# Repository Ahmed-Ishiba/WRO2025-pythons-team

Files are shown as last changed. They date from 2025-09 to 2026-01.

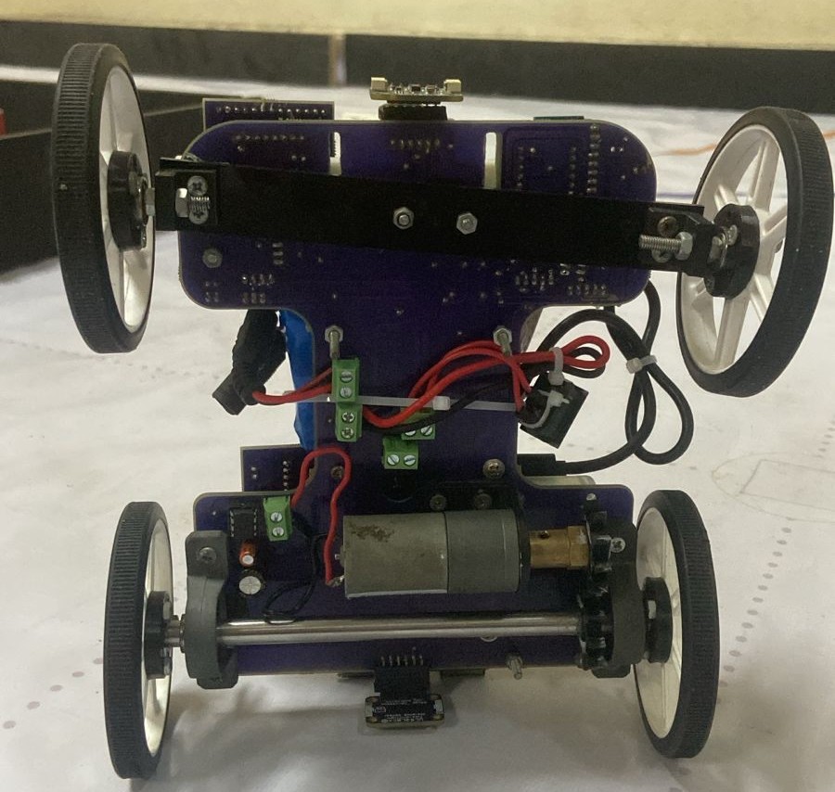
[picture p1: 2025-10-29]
Team&Robot Photos/Undeer_view.jpeg

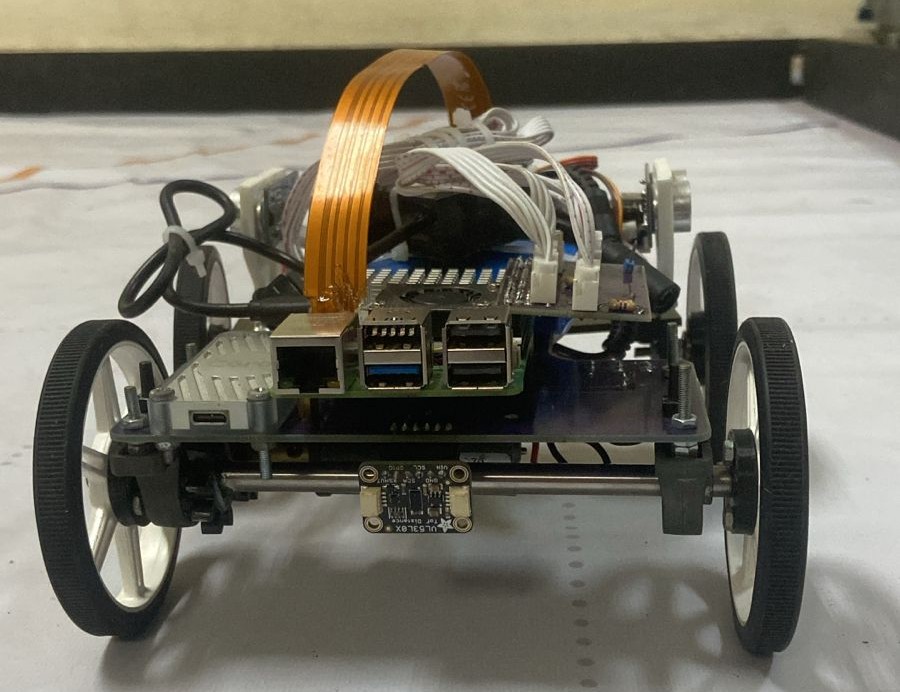
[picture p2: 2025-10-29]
Team&Robot Photos/Back_photo.jpeg

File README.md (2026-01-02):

<p align="center">
mainThepythons-removebg-preview
</p>

<p align="center">
  <a href="https://www.the-pythons.com/" target="_blank">
    
  </a>
  <a href="mailto:ahmedishiba9@gmail.com">
    
  </a>
  <a href="https://github.com/ahmed-ishiba">
    
  </a>
   <a href="https://github.com/Thesuperiornour">
    
  </a>
  <a href="https://github.com/Eyad005">
    
  </a>
  <a href="https://www.youtube.com/@thepythonseg">
    
  </a>
</p>  

Documentation of our self-driving car for the **WRO 2025 Future Engineers** category.

Our team members:
- **Ahmed Ibrahim Elsayed** — Software lead  
- **Eyad Ahmed Nazary** — Electrical lead  
- **Nour Eldin Raoof** — Mechanical design & fabrication  
- **Omar Khaled** — Coach and mentor  

---

## Content

1. [Project Overview](#project-overview)  
    1. [What is WRO?](#what-is-wro)  
    2. [Team Introduction](#team-introduction)  
    3. [Our Mission](#our-mission)  
2. [System Design](#system-design)  
    1. [Robot Architecture](#robot-architecture)  
    2. [Design Philosophy](#design-philosophy)  
    3. [System Diagram](#system-diagram)  
    4. [Bill of Materials](#bill-of-materials)  
3. [Hardware](#hardware)  
    1. [Mechanical](#mechanical)  
    2. [Electrical](#electrical)  
4. [Software](#software)  
    1. [Brief Overview](#brief-overview)  
    2. [Code flow chart](#flow-chart)  
5. [MATLAB Modeling & Simulation](#modelling-and-simulation)  
    1. [Model Overview](#model-overview)  
    2. [Problem Context and Strategy](#problem-context-and-strategy)  
    3. [Modeling and Simulation](#modelling-and-simulation)
        1. [Simulink Logical Model](#simulink-logical-model)
        2. [Complementary Filter Subsystem](#complementary-filter-sub-system)
        3. [Stateflow Diagram](#state-flow-diagram)
        4. [MATLAB Function](#matlab-function)
        5. [Simscape Electrical Model](#simscape-electrical-model)  
    4. [Testing and Verification](#testing-and-verification)  
6. [Testing & Calibration](#testing-and-calibration)
7. [Reproduce Our Robot: Step-by-Step Guide](#reproduce-our-robot)
8. [Future Improvements](#future-improvements)
9. [Team photo](#team-photo)  

## Project Overview

### What is WRO?

WRO (World Robot Olympiad), specifically the **Future Engineers** category, is a competition created to foster passion for STEM. The Future Engineers category is designed for university students. The challenge changes every 3 years, and this year the theme is **autonomous driving**.  
The robot must be designed to drive around a track **completely autonomously**, without external human intervention.

### Team Introduction

We are the **third generation** of *The Pythons* team.  
Our team consists of 3 members and a coach:

1. **Ahmed Ibrahim Elsayed (me):** Software lead — 2nd year, Faculty of Engineering, Alexandria University  
2. **Eyad Ahmed Nazary:** Electrical lead — 1st year, AASTMT  
3. **Nour Eldin Raoof:** Mechanical lead — 3rd year, Faculty of Science, Alexandria University  
4. **Omar Khaled:** Team coach — AASTMT

We have been participating in robotics competitions since **2016**, and we joined The Pythons team in **2017**.

### Our Mission

Our main mission in robotics competitions is to **improve ourselves**, gain experience, and meet like-minded people.  
We specifically enjoy WRO because it **encourages open-source work**, allowing teams to learn from each other, share solutions, and build stronger communities.
.
## System Design:
  ### Robot architecture:   
The main input sources are the camera, ultrasonic sensors to measure distance from walls, Time Of Flight sensors to measure distance from obstacles and parking lot walls, MPU6050 sensor to measure orientation angle for corner rotation and to ensure parallel parking.  
Then the raspberry pi processes these input data and outputs character to KB2040 to control servo and DC motors

  ### Design philosophy:
  When designing our robot we always made sure that our design follows a modular design that is easy to comprehend and troubleshoot, which helps us in improving it with ease, this approach also minimizes time delays that may happen due to fabrication and unfortunate mishaps, this also helps anyone without experience in robotics and future teams to pick up where we left off.
  ### System diagram:  
system_diagram_main drawio

This diagram shows the main components of the robot and how they communicate.  
- The Raspberry Pi 5 acts as the central controller, running the main software and decision-making algorithms.  
- It communicates with ESP32 microcontroller and KB2040 via UART.  
- The KB2040 handles all real-time tasks such as controlling the servo and DC motors through PWM signals.  
-  All controllers share a common power source with independent voltage regulation for stability.

<br>  

  ### Bill Of Materials:   
  
| Component Name | Number of Items | Price (EGP) | Price (USD) |
|---|---|---|---|
| Google Coral Accelerator | x1 | 6,250.00 | 125.00 |
| ESP32 Supermini | x1 | 350.00 | 7.00 |
| KB2040 | x1 | 425.00 | 8.50 |
| Raspberry Pi 5 | x1 | 4,000.00 | 80.00 |
| IMU MPU6050 | x1 | 125.00 | 2.50 |
| Step Down Converter 12V→5V | x1 | 450.00 | 9.00 |
| Wheels | x4 | 473.00 | 9.45 |
| Motor | x1 | 350.00 | 7.00 |
| Servo (180°) | x1 | 150.00 | 3.00 |
| Arducam | x1 | 3,000.00 | 60.00 |
| Step Down Converter 12V→3.3V | x2 | 35.00 | 0.70 |
| 12V Battery | x1 | 450.00 | 9.00 |
| Ultrasonic Sensor | x2 | 45.00 | 0.90 |
| Motor Driver IC | x1 | 100.00 | 2.00 |
| Big Ball Bearings | x2 | 100.00 | 2.00 |
| Small Ball Bearings | x2 | 50.00 | 1.00 |
| PCB Fabrication | x1 | 1,250.00 | 25.00 |
|Time Of Flight sensor | x2 | _ | _ |
| **Total** | — | **17,186.50** | **363.41** |
## Hardware:
This section includes brief overview of hardware section of robot (Mechanical and electrical).  
Each section is explained in detail in it's respective folder  
SLDPRT, DXF and board files are also included in their respective folder to download, print and get down to business.  
  ### Mechanical:
  [Mechanical directory](/Mechanical/)     
  
Robot 3d Design

During the design phase, we chose to stick with a simple structure to save time on fabrication, especially after making a bold decision that I’ll discuss in the next section. Our main focus however was to maximize the steering angles achievable from the servo by creating a fully free movement system, which is vital in turning since we can turn faster and closer to the blocks than other cars. In order to follow the competition's guidelines of using only _**one**_ motor to provide the forward movement to the whole robot we created a gear system to transfer the motor's movement to the rear wheels, also creating a versatile semi movable component mounting system -as seen in the camera mounting- to eliminate the need for refabrication which in turn cuts down the time needed for assembling the robot. 

We also chose big wheels to maximize distance crossed during same revolution this also helps in faster steering.  

  ### Electrical:  
  [Electrical directory](/Electrical/)
3d_pcb  

You might’ve noticed that our PCB has a rather unusual shape — that’s because it is the shape of our mechanical design!  
This brings us to the bold decision I mentioned earlier: we chose to make the base itself the main circuit.  
This approach not only improves stability and reduces overall size by eliminating separate circuit boards, but also makes assembly incredibly straightforward — every component has its exact place.  

But wait — there’s another bold decision! Did you notice there’s no motor driver on our robot?  
That’s right — we built our own motor driver using a dedicated IC and a decoupling capacitor.  
This approach helped us further reduce the robot’s size by eliminating the need for bulky modules like the L298N or Cytron drivers.

## Software:
In this section I will also only provide overview on code and thought process since line-by-line documentation can be found in the [Software directory](/Software/).  

  ### Brief overview:
  For our software and programming I divided it into 3 sections: 
  - Wall tracking
  -  Obstacle Avoidance
  -  Corner detection
  -  Parking
1. Wall Tracking:
   For wall tracking I calculated wall area difference that camera sees and wall difference measured from ultrasonic sensors then used sensor fusion to get accurate data that    I then passed to a PID controller to center the robot all processed on the raspberry pi 5.
   
2. Obstacle Avoidance:
    For obstacle avoidance we used a custom trained yolov8 AI model with 500+ pictures to make sure that the robot detects the traffic signs regardless of environment.
    This approach is better than the traditional image processing approach that relies on the environment since HSV values change according to reflected light.
    Our AI model runs on the google edge TPU to achieve high FPS and faster detection.

     

  https://github.com/user-attachments/assets/0746ed6e-e767-420a-9b96-121c0c189ac0

3. Corner detection:
   For corner detection we used simple image processing algorithms that detect blue and orange strips using the HSV values of each color to apply masks
   
4. Parking:
   IN PROGRESS  
  ### Flow Chart:   

flow_chart drawio

## Modelling and simulation:
  ### Model Overview:  
  Here we will not go into much detail, you can find a detailed explanation, model files and statflow files in the [Modelling and simulation directory](/Modeling%20and%20simulation/)  
  </br>
  When designing our wall centering algorithm we used the simplest algorithm possible due to how hard it is to tune advanced control algorithms like PID or applying filters, however when MathWorks created this award we had no reason not to use it and apply any algorithm we wanted especially after giving us license for the newest MATLAB version for free.  
  </br>
  now we can apply all the algorithms we want and all my crazy ideas, here is what we did:  
  When centering in the previous algorithm we only used the area of the 2 walls seen by our arducam however it was really noisy and changes too fast which is not that good for wall centering, however when we tried to use an ultrasonic sensor the distance readings where precise but the rate at which it changes was really slow  
  </br>
  so now we have 2 methods to measure the same thing each have their pros and cons so we got the idea to fuse them both with a simple weighted sum formula so we can have control over it and ensure it's smoothness  
  
  After we get the result of the formula which measures the deviation of the robot from the center of the lane we then pass it into a PID controller then we take the output of the controller and pass it into a map function that we implemented myself in order to convert the range of the PID output into a range that my servo accepts(from 0 to 180)  
  
  ### Problem context and strategy:  
  the main challenges that we faced were:  
  - Creating the weighted sum formula and tuning the weights
  - Tuning the PID
  - Making sure the map function works correctly
  - and a problem that we realised later is that I don't know how to test this!
  - simulating our electrical system on simscape electrical  

  As for our strategy:   
  1. we started by writing pseudo code for my algorithm and knew it's building blocks
  2. For simplicity we divided this algorithm into 5 parts: the complementary filter, the PID controller, the map function, creating a stateflow diagram and simulating the circuit we then tackled each in this order
  3. we then decided what MathWorks products help with this which were: Simulink for creating a subsystem for my filter and use it's wide variety of blocks to save time on implementing a PID algorithm from scratch, MATLAB for writing code of our mapping function, simscape electrical for simulating my electrical system and stateflow for creating a diagram of my algorithm using states  
  </br>   
  Using MATLAB, Simulink, simscape and state flow saved so much time and were extremely helpful   

  - using MATLAB for writing the mapping code was extremely easy especially with MATLAB's easy syntax
  - Simulink was by far the best tool we used because not only can we tune algorithms and filters without needing any hardware we can just tune it with only clicking one button! not to mention the clear modular look that helped me troubleshoot where exactly our model went wrong, the graphing that helps us understand the behaviour of our robot and derive meaningful data from it and realizing logical problems in minutes that would've taken days to realize
  - stateflow was really helpful in dividing the algorithm like a flow chart but much briefly, helped us in verifying my code since the code is divided into states just like stateflow and it also helped us in verifying condition if changing states and overall is a vital tool
  - simscape electric was used for simulating our circuit and finding out stall current, max current draw and we used it to correct our choice of battery since we kept having power issues but using simscape we corrected a mistake that would've cost us the competition, this is also a tool that we would definitely use for future robotics projects

  ### Modelling and simulation:  
  #### Simulink logical model:  
  
  now for the main model as I said everything is explained in detail in the [Modelling directory.](/Modeling%20and%20simulation/)  
  simulink_model  

  This is the main model and as you can see we take input from 2 sources that somewhat measure the same thing then pass it into our complementary filter that outputs an estimated deviation from the center of the lane and passes it to a PID controller and finally map it to servo range using the map function and send it to the servo  
  
 this algorithm is from my perspective as simple as it gets while at the same time maintaining it's simplicity for fast and easy troubleshooting (not that there is room for error after tuning it)  

#### Complementary filter sub-system:  

 For the complementary filter we created a sub-system for it which is by far the most useful feature in simulink since the logic for the filter is very confusing when put with the main system, here is the diagram for the complementary filter (explained in detail in the modelling directory):  
 
  filter_subsystem  

#### State-flow diagram:   

  Here is the stateflow diagram for you to understand how our code is divided  

  stateflow_chart     

#### MATLAB function:   

Here is the mapping function we implemented which is just a mathematical formula nothing too complicated   

mapping_function

#### Simscape electrical model:   
We used simscape electrical to measure our maximum ampere consumption, required voltage and suitable battery capacity, here is a photo of our model:   

model

  ### Testing and verification:   
  #### Testing Logical model:   
  
  For testing this model we had to think and come up with ideas we then came to the conclusion to use the simulink function generator  
  
  we used a sin wave to simulate changing input and we of course got an output in shape of sin wave which is both scientifically and physically correct since this model is considered a linear time-invariant system so only the amplitude changes and physically correct since when error increases from the setpoint(the rise of the sine wave) the output should also increase to compensate and correct this error  

  model_using_sine  

  complementary_filter_and_pid  

this is the graph of the complementary filter and the PID controller and above it is the model but we used the sin generator as the input.

  

This is the output(servo degree) resulting from the model and as you can see it changes reasonably with the changing the input both following the same graph  

</br>
We also used step function generator to simulate specific cases that I encountered when working on my robot and coincidentally found them

model_using_step  

step_output

this is the output (servo degree) resulting from our model and above it is the model using the step function generator  

</br>

#### Testing the electrical model:  

As for testing our electrical model it was as easy as hitting run then seeing the output voltage and current intensity on our scope  

volt_intemsity  

 As you can see we got a max current draw of 7 Amps and voltage of approximately 11.1 volts so we made our decision for battery type by dividing available battery capacities on the internet by the max current and getting how long it will last.  

## Testing and calibration:
After completing the robot assembly, we performed a series of tests to ensure that every subsystem was functioning correctly.
We ran the test scripts located in the [Software Testing Directory](/Software/System%20Testing/)

- Communication between the microcontrollers and sensors
- Sensor testing and calibration
- Motor operation and direction control
- Servo steering response
- Camera functionality and data transmission

## Reproduce Our Robot:  
A [Raspberry pi setup script](/raspberrypi_setup.sh) is included that setups all required packages 
1. First start with the main body of robot (after buying components of course)
2. Fabricate the pcb since this is the body or if you want to wire everything and don't need a pcb just download our solidworks files and cnc cut it
3. assemble the robot by connecting everything to the pcb like labeled in our fusion360 file or connect using jumper wires
4. setup the raspberry pi and enable i2c and uart
5. clone this repo on raspberry pi
6. test the system using the files in the [Software testing directory](/Software/System%20Testing/)
7. After making sure every component in the system is running normally, run the main code
8. Now you have a working WRO Future engineers self-driving car!

## Future improvements:
In the future if we participate again and for other teams looking at this repo here are some improvements I wished to implement:
- Use better sensor fusion algorithms
- Create a Simulink environment specifically for this competition like the one in robotics playground
- Better weight distribution in the robot design
- Put built-in voltage sensor
- add cloud-based data logging for better debugging
- create a GUI that combine camera frame and terminal output (looks cool no other reason)
## Team photo:  



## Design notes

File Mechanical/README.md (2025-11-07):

# Mechanical design of robot:
## Drive System 
The Mechanical part is the first part in the process of the robot's creation, in the WRO Future Engineers category there are certain design regulating rules like size must not excede 30x30cm or that the robot's 
weight must not excede 3kg and the robot must be driven wholly by one motor while these regulations seem easily applicable the last one is not to overcome that challenge we created a fully original gear system that 
features two gears that have been designed from scratch and modified specifically for our needs to provide forward motion for the robot.
Robot Rear System

### Steering System 
In the previous section i mentioned the regulation that says that whole robot's drive must be powered by just __*one*__ motor but that doesnt say the same for the steering system, we created a 120 degree of freedom steering system all connected to one servo motor, this ingenius design is very effective against even the sharpest of turns.



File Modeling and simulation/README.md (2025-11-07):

# Detailed explanation of each model 

# Table of content:  

1. [Electric model](#electric-model)
2. [Map function](#map-function)
3. [Simulink model](#simulink-model)
4. [Cool animation using robotics playground](#animation-using-robotics-playground)

## Electric model:

model  

This model represents the electrical power distribution of a small robotic system. It includes a DC battery, a buck converter for regulated low-voltage supply, an H-Bridge driving a DC motor, a servo motor subsystem, and load models representing microcontrollers and sensors. The goal is to simulate real power consumption, voltage drops, and motor behavior under different load conditions.

### 🟦 Overview of Simscape

Simscape is a MATLAB/Simulink toolbox that allows modeling using physical components rather than manual equations. Components are connected using physical conserving ports (e.g., electrical +/− terminals), ensuring simulations follow real laws like Kirchhoff’s Current/Voltage Law and mechanical rotational dynamics.  

This is useful for:   

- Testing system behavior before hardware assembly.  

- Observing current and voltage profiles.

- Evaluating different power configurations.

- Detecting instability or saturation in motor loads.

### 🔌 System Components and Their Roles   

| **Component** | **Purpose in the System** | **Important Parameters to Configure** |
| --- | --- | --- |
| DC Battery | Supplies the main power to the system, representing the real robot battery. | Nominal voltage, internal resistance, capacity (optional). |
| Buck Converter | Steps down battery voltage to a lower regulated voltage for electronics and low-power devices. | Output voltage, inductor value, capacitor value, switching frequency. |
| Constant Power Load | Models microcontrollers and sensors that draw nearly constant power regardless of voltage. | Power consumption (W), minimum operating voltage. |
| H-Bridge | Controls motor direction and speed using PWM input signals. | Control mode (PWM/Logic), supply voltage, dead-time/shoot-through protection. |
| DC Motor | Converts electrical power into mechanical rotational power. Represents drivetrain motors. | Armature resistance, back-EMF constant, rated torque, inertia. |
| Servo Motor | Provides controlled angular positioning (steering / joints). Modeled as DC motor with internal control feedback. | Supply voltage, stall torque, rated speed, control input range (e.g., angle). |
| Current Sensor | Measures current drawn by a component for monitoring and analysis in simulation. | No parameters (acts as a probe). |
| Voltage Sensor | Measures voltage across nodes (e.g., battery output, motor terminals). | No parameters (acts as a probe). |
| Scope | Displays real-time signals from sensors during simulation. | Number of traces, time display range. |

### How to Recreate the Model Step-By-Step

1. Start Simscape Environment
2. Open Simulink → Simscape → Simscape Electrical → Specialized Power Systems.
3. Add the Power Source
4. Place DC Battery (Simscape → Electrical → Sources).
5. Set nominal voltage matching your real battery.
6. Build the Power Distribution Path
7. Add Buck Converter (Simscape → Electrical → Converters).
8. Connect battery output → buck input.
9. Place Voltage Sensor after buck output to monitor regulated voltage.
10. Add Load for Microcontroller
11. Insert Constant Power Load block.
12. Connect to the buck output to represent electronics load.
13. Add Drive Motor Path
14. Insert H-Bridge and DC Motor blocks.
15. Connect H-Bridge output terminals to motor armature.
16. Drive the H-Bridge with a PWM signal (from a Pulse Generator or control logic).
17. Add Servo Motor
18. Place a Servo DC Motor or build a small subsystem using:

    DC motor + position control + gear constraint.

19. Connect it to the same or separate power bus depending on design.
20. Run the Simulation

## Map function:  

```matlab
function mapped_value = map_value(value)
%MAP_VALUE maps a value from one range to another

    from_low=-50;
    from_high= 50;
    to_low=30;
    to_high=160;
    % Avoid division by zero
    if (from_high - from_low) == 0
        mapped_value = to_low;
        return;
    end

    % mapping equation
    mapped_value = (value - from_low) / (from_high - from_low) * ...
                   (to_high - to_low) + to_low;
end
```

What the Code Does:  
1. Defines the input range

```matlab
from_low = -50;
from_high = 50;

```
2. Defines the output (desired) range
```matlab
to_low = 30;
to_high = 160;

```

3. Applies the linear mapping formula
```matlab
mapped_value = (value - from_low) / (from_high - from_low) * ...
               (to_high - to_low) + to_low;
```

### Simulink model:   

model_using_sine

This is the main model with input sine wave to simulate the inputs 
- The input camera is passed through a gain to *convert* it to distance area this gain is through trial and error I then pass it to the filter block
- The ultrasonic readings are subtracted to get difference
- After the filter block I pass it to the PID controller tuned using the PID tuner app
- Then map it and display it on the scope

#### Filter sub-system:   

filter_subsystem    

This diagram just calculates the weighted average using the formula:   



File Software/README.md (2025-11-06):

# Raspberry pi system:
our algorithm is divided into 2 sections: centering the robot in the track to avoid walls, detecting the boxes and move accordingly
## centering of robot:
For centering the robot we used combination of algorithms: centering using the ultrasonic distance readings, measuring wall area and getting diffrence to know what wall is closer then combining the 2 using our own complementary filter 

### how do we combine 2 fundementally different measurements like area and distance?
well I have a pretty nice analogy, if your eyes were closed and you are in a maze with another person and your task was to go to find this person knowing that this person will shout every 3 seconds or so how will you find him?  

well that is easy you can use your hands to feel the maze and see where to go and at the same time hear the shouting of this person to know if you are getting closer or farther, well now you have used 2 different senses to know where to go.

### What is this complementary filter?

A complementary filter in general is a way to filter the noisy inputs or inaccurate in order to produce stable output

how does it work?  

it realies on a mathematical formula known as **weighed average** this formula tells us that if you have 2 inputs that somewhat have same nature and measure same thing you can combine them in a way where you can *trust* an input more than the other thus calling it a weighted average because you provide weight to each input symbolizing how much you trust said input

complementary filter formula:  


knowing that the alpha is the weight we decide  

implemented in code as: 
```python
def complementary_filter(wall_area_diff, ultrasonic_diff, alpha=0.7):
    """
    Complementary filter for fusing two distance-related signals.
    """
    return alpha * wall_area_diff + (1 - alpha) * ultrasonic_diff

# Example
filtered_value = complementary_filter(0.35, 0.32, alpha=0.7)
print("Filtered Output:", filtered_value)

```  
### PID controller:  
A PID controller (Proportional–Integral–Derivative controller) is a feedback control method used to minimize the error between a desired setpoint and the actual measured value.
It does this by calculating a correction value made of three components:

- Proportional (P): Reacts to the current error

- Integral (I): Accumulates past errors to eliminate steady-state offset

- Derivative (D): Predicts future error based on the rate of change

By combining these three terms, the PID controller can respond quickly, remain stable, and reduce long-term error.  

PID formula:  

$$
e(t) = \text{setpoint} - \text{measurement}
$$

$$
u(t) = K_p \, e(t) \+\ K_i \int_{0}^{t} e(\tau)\ d\tau \+\ K_d \frac{d e(t)}{dt}
$$

code implementation:  
```python
class PIDController:
    def __init__(self, Kp, Ki, Kd):
        self.Kp = Kp
        self.Ki = Ki
        self.Kd = Kd
        self.integral = 0
        self.prev_error = 0

    def compute(self, setpoint, measurement, dt):
        # Calculate error
        error = setpoint - measurement
        
        # Proportional term
        P = self.Kp * error
        
        # Integral term
        self.integral += error * dt
        I = self.Ki * self.integral
        
        # Derivative term
        derivative = (error - self.prev_error) / dt
        D = self.Kd * derivative
        
        # Save error for next cycle
        self.prev_error = error
        
        # PID output
        return P + I + D

# Example usage:
pid = PIDController(Kp=1.2, Ki=0.4, Kd=0.05)
output = pid.compute(setpoint=1.0, measurement=0.85, dt=0.02)
print("PID Output:", output)

```
## Detecting the boxes:
For detecting the boxes we used a custom trained Ultralytics YOLO V8, it has proven to be very reliable, as for taking action on where are the boxes and how to maneuver them we get the x-coordinate of box to decide type of turning motion(hard or normal turn) and get the height of robot to know if we are close or not to the box 

## Flow chart of code:  

 flow_chart drawio

### General flow of code:
First we check for corners and give it highest priority, then we check for boxes and lastly check for walls and this is the lowest priority  

Untitled Diagram drawio

# KB2040 system:
The code used in the KB2040 microcontroller is just simple motor control and servo control which can be included on the raspberry pi but we decided to sperate them for simplicity and not to put too much load on the raspberry pi

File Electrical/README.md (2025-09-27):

# Electrical schematics and boards:

The following are schematic files that showcase the circuit of our robot and the board files are used to fabricate the PCB

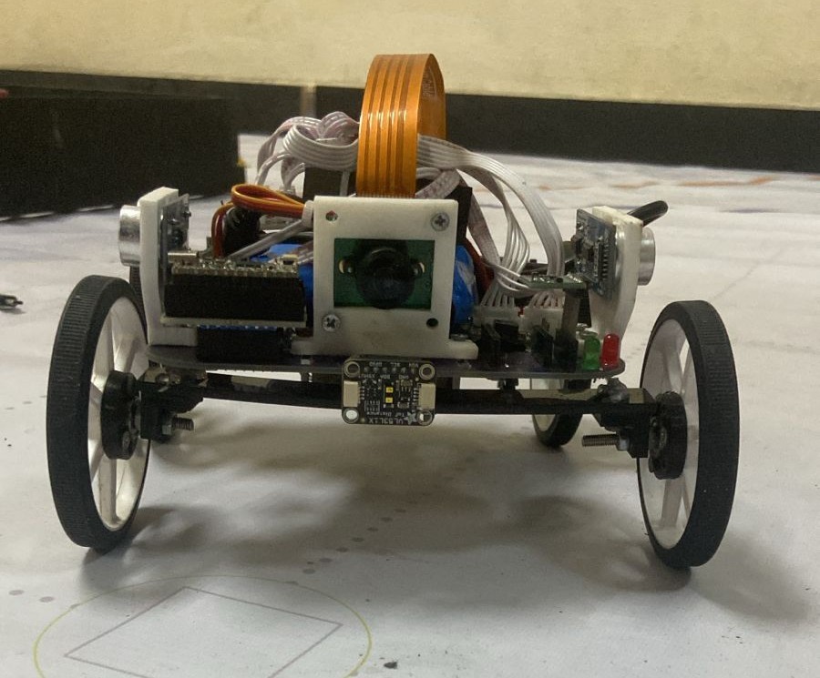
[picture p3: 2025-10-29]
Team&Robot Photos/Front_view.jpeg

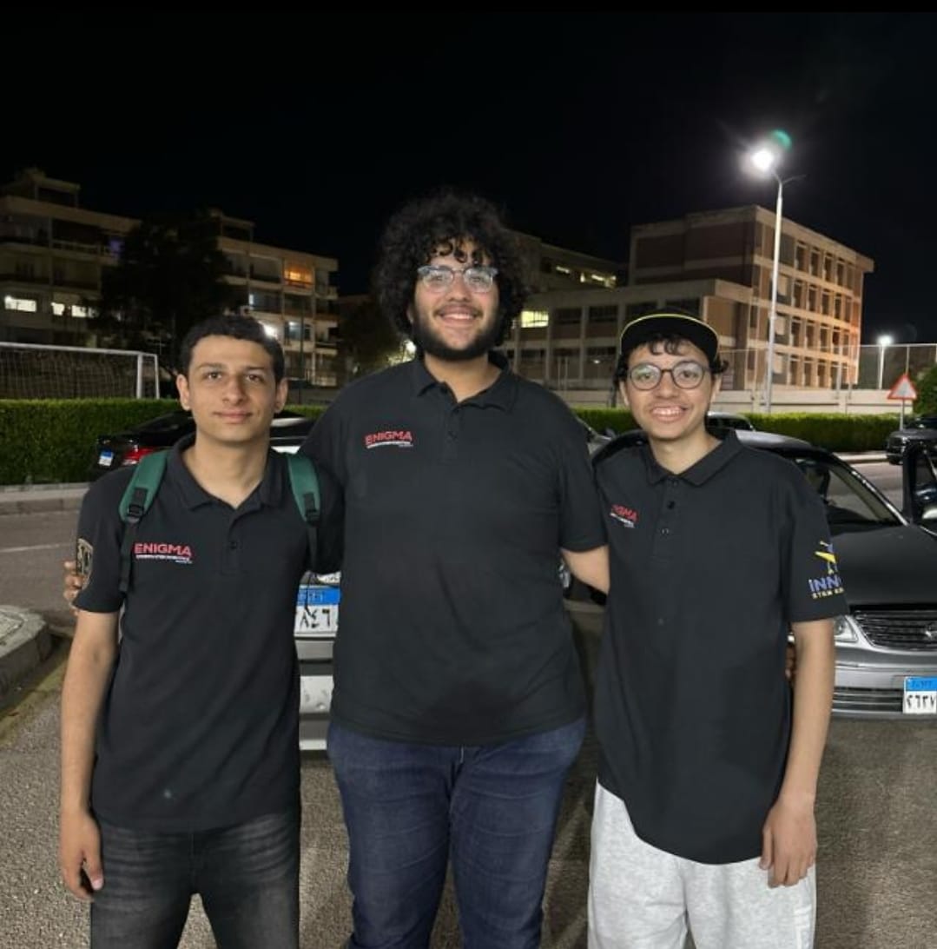
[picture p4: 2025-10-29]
Team&Robot Photos/Team_Photo.jpeg

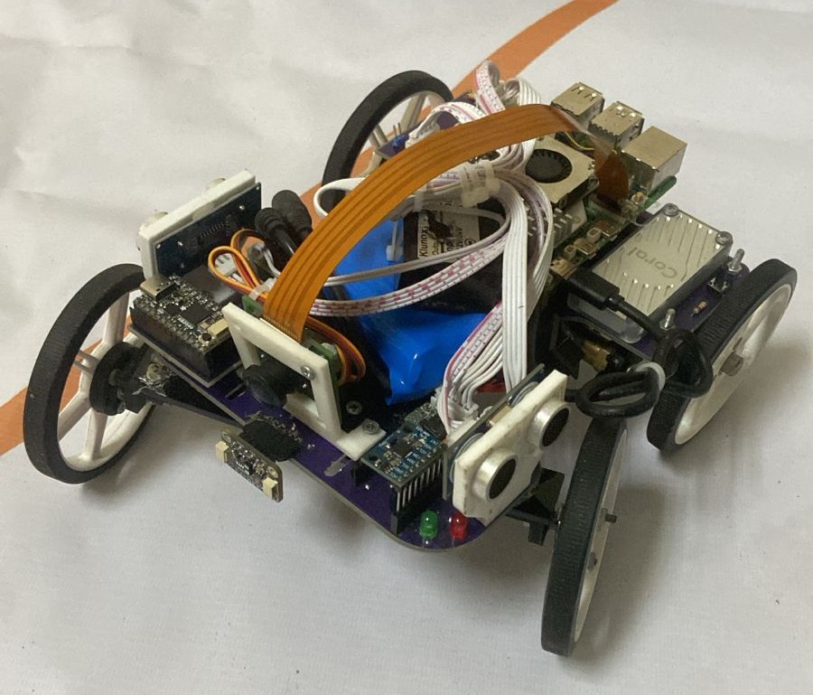
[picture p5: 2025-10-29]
Team&Robot Photos/ISO photo.jpeg

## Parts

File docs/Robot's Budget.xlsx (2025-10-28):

The Robot's Budget
Components Name: | Number Of Iteams | Price in USD: | Price in EGP:
Google Coral Acclerator | x1 | EGP 6250.00 | USD 125.00
ESP32 Supermini | x1 | EGP 350.00 | USD 7.00
KB2040 | x1 | EGP 8.50 | USD 425.00
Raspberry Pi 5 | x1 | EGP 4000.00 | USD 80.00
Imu MPU6050 | x1 | EGP 125.00 | USD 2.50
Step Down Convertor 12V-5V | x1 | EGP 450.00 | USD 9.00
Wheels | x2 | EGP 473.00 | USD 9.45
Motor | x1 | EGP 350.00 | USD 7.00
Servo (180Degree) | x1 | EGP 150.00 | USD 3.00
Arducam | x1 | EGP 3000.00 | USD 60.00
Step Down Convertor 12V-3.3V | x2 | EGP 35.00 | USD 0.70
12V Battery | x1 | EGP 450.00 | USD 9.00
Ultrasonic | x1 | EGP 45.00 | USD 0.90
Motor Driver ic | x1 | EGP 100.00 | USD 2.00
Big Ball Bearings | x2 | EGP 100.00 | USD 2.00
Small Ball Bearings | x2 | EGP 50.00 | USD 1.00
Pcb Fabrication | x1 | EGP 1250.00 | USD 25.00
 | Total: | EGP 17186.50 | USD 768.55

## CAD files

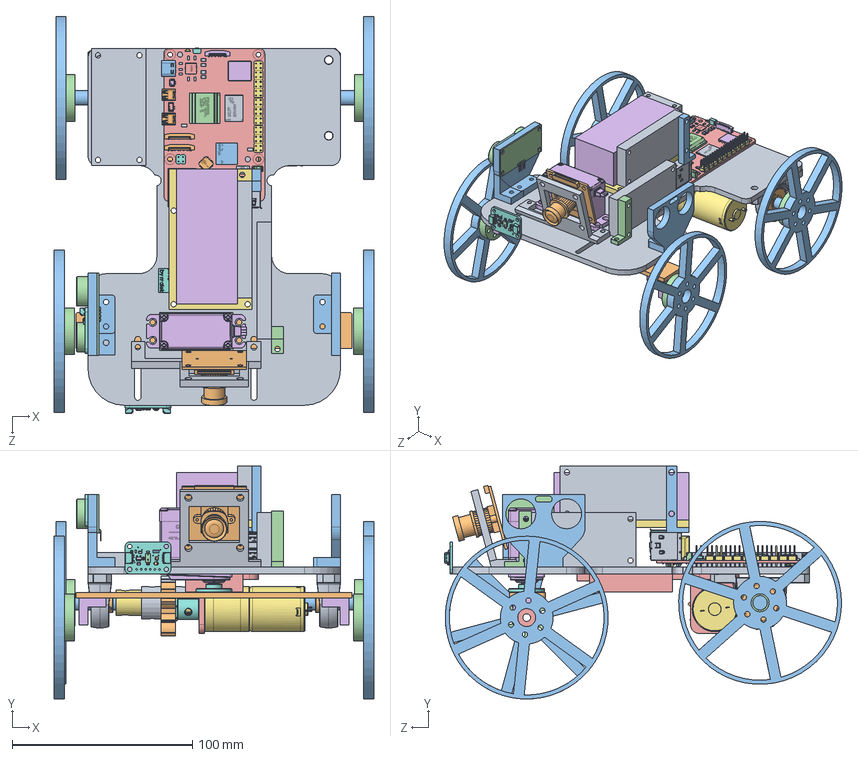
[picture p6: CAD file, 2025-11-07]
Mechanical/!Assem_v2.SLDASM
177.5 x 129.2 x 220.2 mm
Base_v2
front wheel axle_v2
dc motor wheel_v2 x 4
3d part coupler thingy_v2 x 2
Mini Ball Bearing_v2 x 2
3d part 90_v2 x 2
12 V MOTOR - Copy_v2
COUPLER - Copy_v2
KP08_v2 x 2
608RS_v2 x 2
Back axle_v2
3d part coupler thingy for drive_v2 x 2
motor holder 2 - Copy_v2
DS3218MG MS24 Digital Servo 270
Shaft Coupler x 2
servo horn.step
Shaft Gear
Coupler Gear
arduholder_v2
ArduCam_M12Lens.step
VL6180X_PART1.step
VL6180X_PART2.step
VL6180X_PART3.step
VL6180X_PART4.step
VL6180X_PART5.step x 12
Lens 1.step
Lens 2.step
Lens 3.step
Cathode.step
Anode.step
Cathode Bar.step
Body.step
Printed Circuit Board.step
SOT23-5.step
SOT23-6.step
YC164_RESPACK.step
LED 0603 single color.step
CAPC-0603-T0.9-BN.step
CAPC-0805-T0.95-BN.step x 2
RESC-0603.step x 3
qwicc.step x 2
Ultrasonic Holder_v2
Ultrasonic Sensor HC-SR04
Buck_v2
Smaller Battery
Smaller Battery Plate
Switch KCD1-11
Coral Accelerator_v2 x 3
CARD_SLOT_METAL_PIN.STEP
SD_CARD_V1.STEP
PART3_V1.STEP
PLATE_RASPBERRY_PI_5.STEP
METAL_PLATE..STEP
GIGABIT_ETHERNET_PORT.STEP
2xUSB_3.0_PORT.STEP
2xUSB_2.0_PORT.STEP
FEMALE_MICRO_HDMI_CONNECTOR.STEP x 2
FEMALE_USB_CONNECTOR.STEP
STOCK_1.STEP
STOCK_2.STEP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

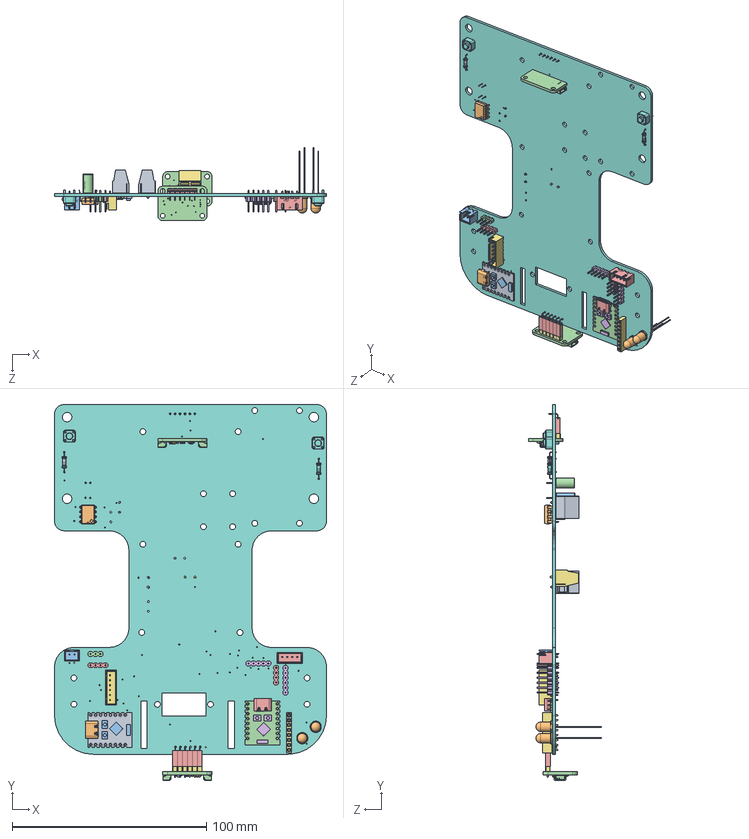
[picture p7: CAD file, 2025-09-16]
Mechanical/WRO_2025 PCB.SLDASM
140.0 x 193.5 x 37.8 mm
Board c3mini.step
USB C.step
components (other)^ESP32-C3 SuperMini.step
Board c3mini (1).step
USB C (1).step
components (other)^ESP32-C3 SuperMini (1).step
8er Pin Header Female.step
VL6180X_PART1.step.STEP.step
VL6180X_PART2.step.STEP.step
VL6180X_PART3.step.STEP.step
VL6180X_PART4.step.STEP.step
VL6180X_PART5.step.STEP.step x 12
Lens 1.step.STEP.step
Lens 2.step.STEP.step
Lens 3.step.STEP.step
Cathode.step.STEP.step
Anode.step.STEP.step
Cathode Bar.step.STEP.step
Body.step.STEP.step
Printed Circuit Board.step.STEP.step
SOT23-5.step.STEP.step
SOT23-6.step.STEP.step
YC164_RESPACK.step.STEP.step
LED 0603 single color.step.STEP.step
CAPC-0603-T0.9-BN.step.STEP.step
CAPC-0805-T0.95-BN.step.STEP.step x 2
RESC-0603.step.STEP.step x 3
qwicc.step.STEP.step x 2
frame_H254.step x 6
pin-90deg.step x 6
1x06 connector.step.STEP.step
VL6180X_PART1.step.STEP (1).step
VL6180X_PART2.step.STEP (1).step
VL6180X_PART3.step.STEP (1).step
VL6180X_PART4.step.STEP (1).step
VL6180X_PART5.step.STEP (1).step x 12
Lens 1.step.STEP (1).step
Lens 2.step.STEP (1).step
Lens 3.step.STEP (1).step
Cathode.step.STEP (1).step
Anode.step.STEP (1).step
Cathode Bar.step.STEP (1).step
Body.step.STEP (1).step
Printed Circuit Board.step.STEP (1).step
SOT23-5.step.STEP (1).step
SOT23-6.step.STEP (1).step
YC164_RESPACK.step.STEP (1).step
LED 0603 single color.step.STEP (1).step
CAPC-0603-T0.9-BN.step.STEP (1).step
CAPC-0805-T0.95-BN.step.STEP (1).step x 2
RESC-0603.step.STEP (1).step x 3
qwicc.step.STEP (1).step x 2
frame_H254 (1).step x 6
pin-90deg (1).step x 6
1x06 connector.step.STEP (1).step
SW_BUTT-2.step x 2
DBCONN-1X2.step x 2
LED_WP7113SRD_D.step x 2
1X02.step
1X03.step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

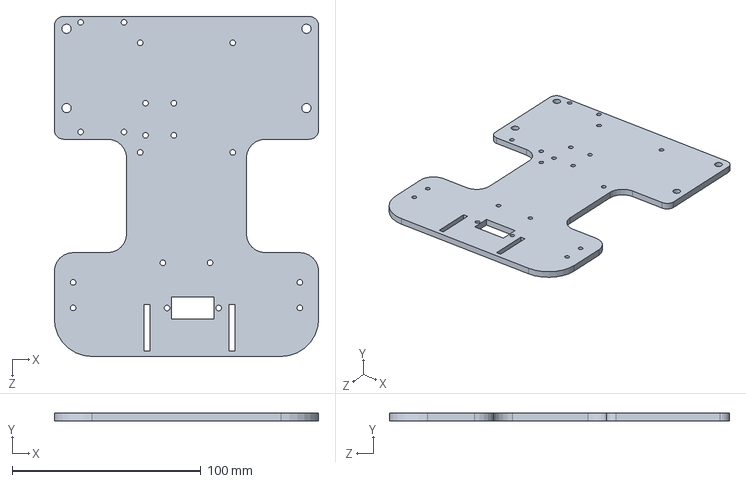
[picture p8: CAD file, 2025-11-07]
Mechanical/Base_v2.SLDPRT
140.0 x 4.00 x 180.0 mm

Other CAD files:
Mechanical/Base.SLDPRT

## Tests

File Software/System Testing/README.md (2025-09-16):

# Codes used for testing the system:

Test the following:
- Serial communication
- motor movments
- ultrasonic reading
- IMU reading
- camera test

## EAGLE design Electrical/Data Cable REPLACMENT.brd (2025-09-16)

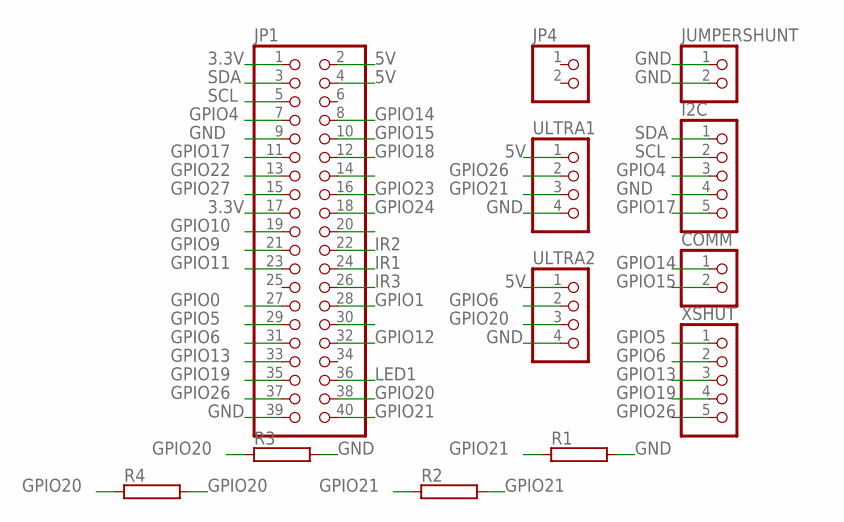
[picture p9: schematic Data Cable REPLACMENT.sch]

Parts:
COMM: PINHD-1X2; 1X02
I2C: PINHD-1X5; 1X05
JP1: PINHD-2X20; 2X20
JP4: PINHD-1X2; 1X02
JUMPERSHUNT: PINHD-1X2; 1X02
R1, R2, R3, R4: RHPS58; HPS58
ULTRA1, ULTRA2: PINHD-1X4; 1X04
XSHUT: PINHD-1X5; 1X05

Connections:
3.3V: JP1.1, JP1.17
5V: JP1.2, JP1.4, ULTRA1.1, ULTRA2.1
GND: I2C.4, JP1.9, JP1.39, JUMPERSHUNT.1, JUMPERSHUNT.2, R1.2, R3.2, ULTRA1.4, ULTRA2.4
GPIO0: JP1.27
GPIO1: JP1.28
GPIO4: I2C.3, JP1.7
GPIO5: JP1.29, XSHUT.1
GPIO6: JP1.31, ULTRA2.2, XSHUT.2
GPIO9: JP1.21
GPIO10: JP1.19
GPIO11: JP1.23
GPIO12: JP1.32
GPIO13: JP1.33, XSHUT.3
GPIO14: COMM.1, JP1.8
GPIO15: COMM.2, JP1.10
GPIO17: I2C.5, JP1.11
GPIO18: JP1.12
GPIO19: JP1.35, XSHUT.4
GPIO20: JP1.38, R3.1, R4.1, R4.2, ULTRA2.3
GPIO21: JP1.40, R1.1, R2.1, R2.2, ULTRA1.3
GPIO22: JP1.13
GPIO23: JP1.16
GPIO24: JP1.18
GPIO26: JP1.37, ULTRA1.2, XSHUT.5
GPIO27: JP1.15
IR1: JP1.24
IR2: JP1.22
IR3: JP1.26
LED1: JP1.36
SCL: I2C.2, JP1.5
SDA: I2C.1, JP1.3

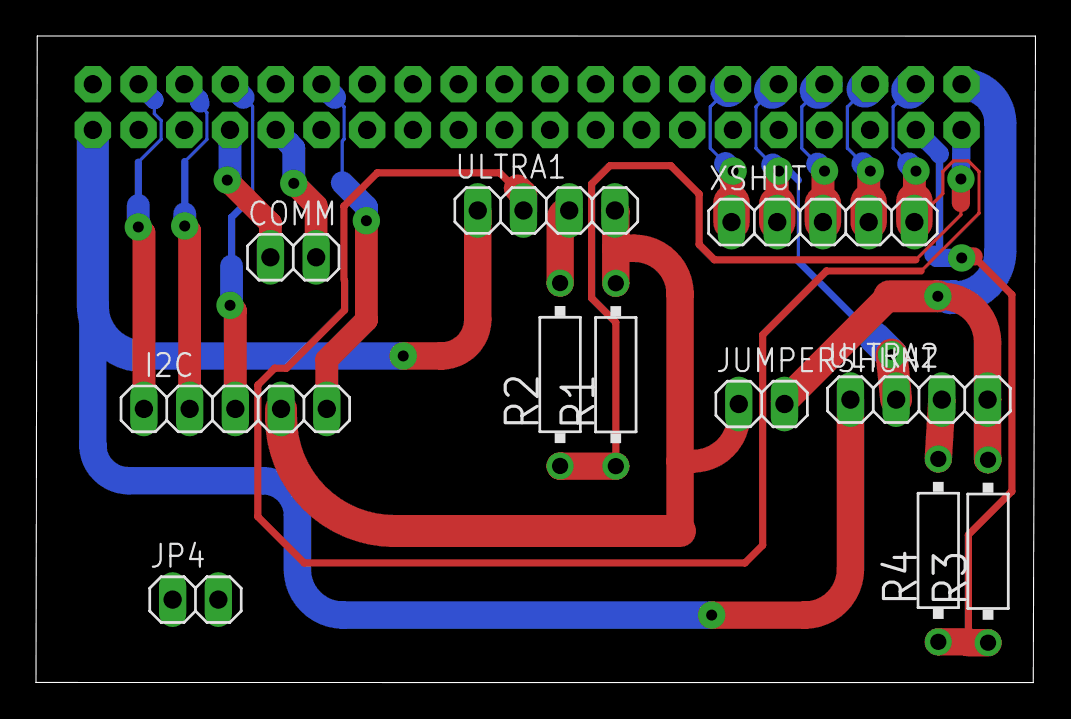
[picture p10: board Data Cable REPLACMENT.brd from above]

Board: 2 copper layers, 55.5 x 35.9 mm, 12 parts (1 on the bottom side), 16 nets.

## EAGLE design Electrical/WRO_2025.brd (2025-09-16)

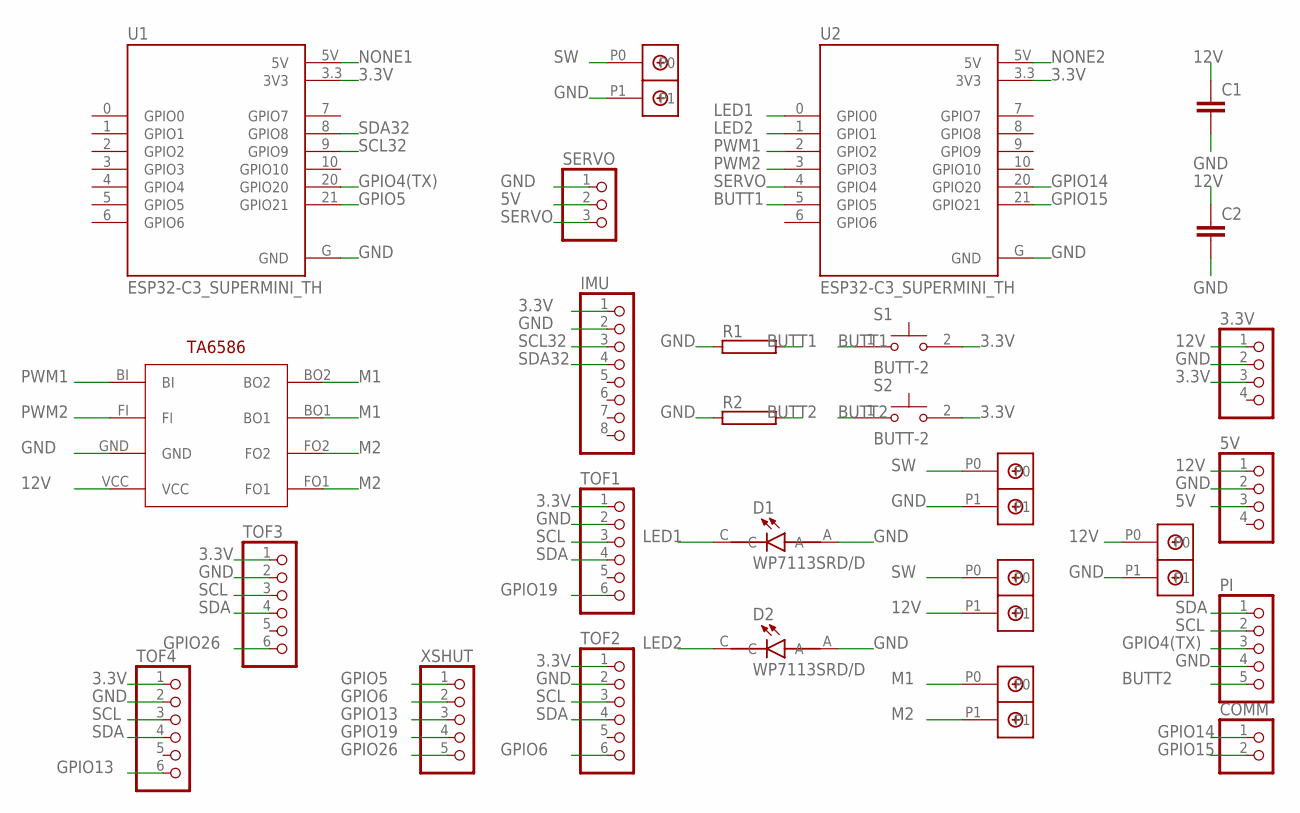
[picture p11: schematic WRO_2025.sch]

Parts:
3.3V, 5V: PINHD-1X4; 1X04
C1, C2: C2,5-3; C2.5-3
COMM: PINHD-1X2; 1X02
D1, D2: WP7113SRD/D; LED_WP7113SRD/D
IMU: PINHD-1X8; 1X08
PI: PINHD-1X5; 1X05
R1, R2: RHPS58; HPS58
S1, S2: BUTT-2; SW_BUTT-2
SERVO: PINHD-1X3; 1X03
TOF1, TOF2, TOF3, TOF4: PINHD-1X6; 1X06
U1, U2: ESP32-C3_SUPERMINI_TH; MODULE_ESP32-C3_SUPERMINI_TH
U$1, U$2, U$3, U$5, U$6: DBCONN-1X2
U$4: TA6586; TA6586-FOOTPRINT
XSHUT: PINHD-1X5; 1X05

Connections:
3.3V: 3.3V.3, IMU.1, S1.2, S2.2, TOF1.1, TOF2.1, TOF3.1, TOF4.1, U1.3.3 (3V3), U2.3.3 (3V3)
5V: 5V.3, SERVO.2
12V: 3.3V.1, 5V.1, C1.1, C2.1, U$2.P1, U$4.VCC, U$5.P0
BUTT1: R1.2, S1.1, U2.5 (GPIO5)
BUTT2: PI.5, R2.2, S2.1
GND: 3.3V.2, 5V.2, C1.2, C2.2, D1.A, D2.A, IMU.2, PI.4, R1.1, R2.1, SERVO.1, TOF1.2, TOF2.2, TOF3.2, TOF4.2, U1.G (GND), U2.G (GND), U$1.P1, U$4.GND, U$5.P1, U$6.P1
GPIO4(TX): PI.3, U1.20 (GPIO20)
GPIO5: U1.21 (GPIO21), XSHUT.1
GPIO6: TOF2.6, XSHUT.2
GPIO13: TOF4.6, XSHUT.3
GPIO14: COMM.1, U2.20 (GPIO20)
GPIO15: COMM.2, U2.21 (GPIO21)
GPIO19: TOF1.6, XSHUT.4
GPIO26: TOF3.6, XSHUT.5
LED1: D1.C, U2.0 (GPIO0)
LED2: D2.C, U2.1 (GPIO1)
M1: U$3.P0, U$4.BO1, U$4.BO2
M2: U$3.P1, U$4.FO1, U$4.FO2
NONE1: U1.5V
NONE2: U2.5V
PWM1: U2.2 (GPIO2), U$4.BI
PWM2: U2.3 (GPIO3), U$4.FI
SCL: PI.2, TOF1.3, TOF2.3, TOF3.3, TOF4.3
SCL32: IMU.3, U1.9 (GPIO9)
SDA: PI.1, TOF1.4, TOF2.4, TOF3.4, TOF4.4
SDA32: IMU.4, U1.8 (GPIO8)
SERVO: SERVO.3, U2.4 (GPIO4)
SW: U$1.P0, U$2.P0, U$6.P0

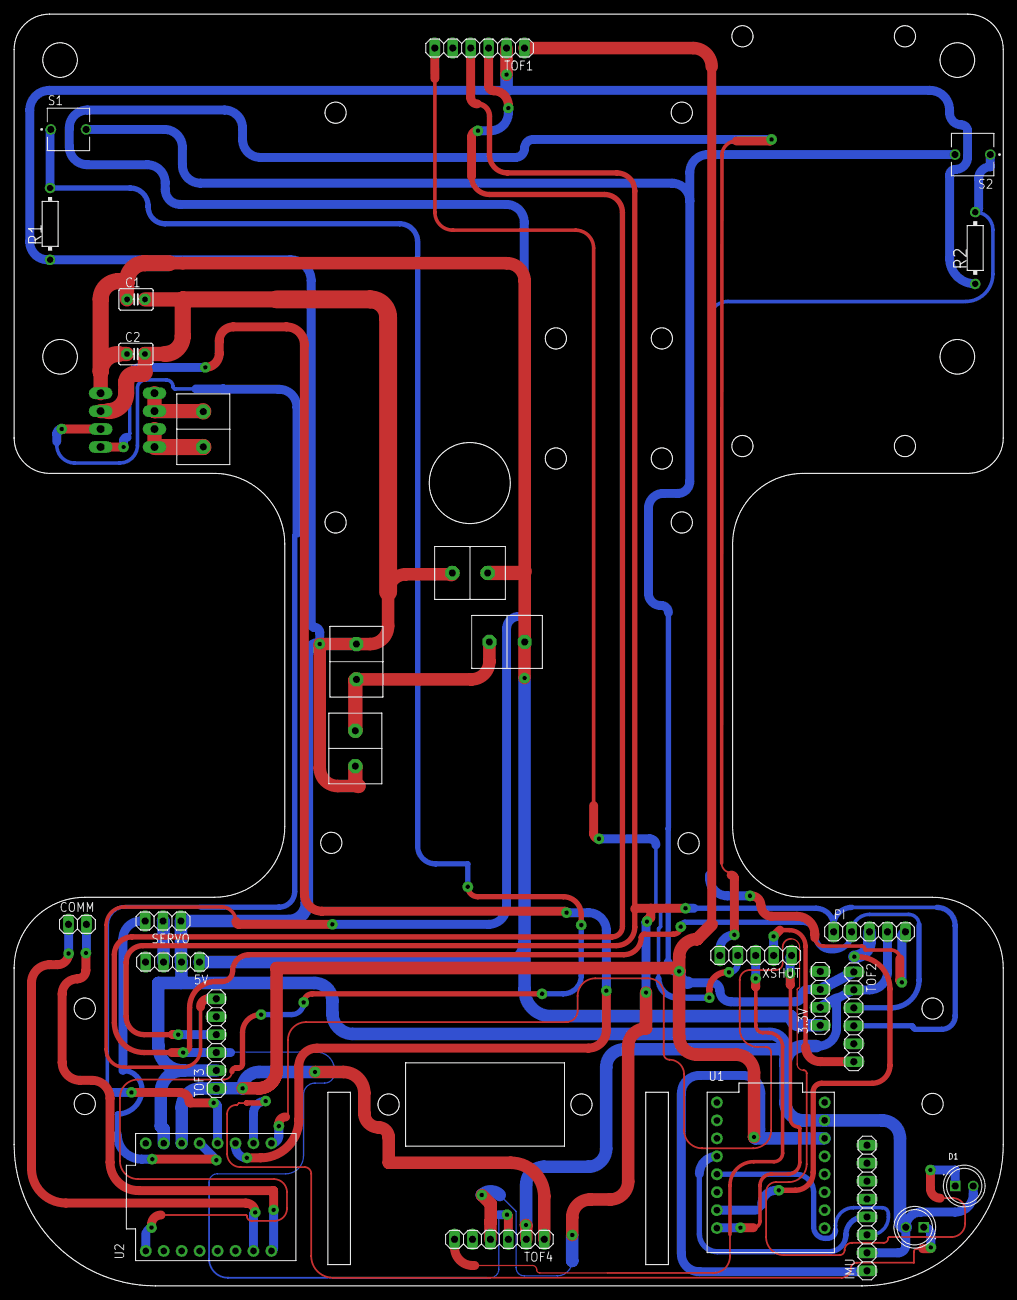
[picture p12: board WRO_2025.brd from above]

Board: 2 copper layers, 140.0 x 180.0 mm, 27 parts (1 on the bottom side), 26 nets.

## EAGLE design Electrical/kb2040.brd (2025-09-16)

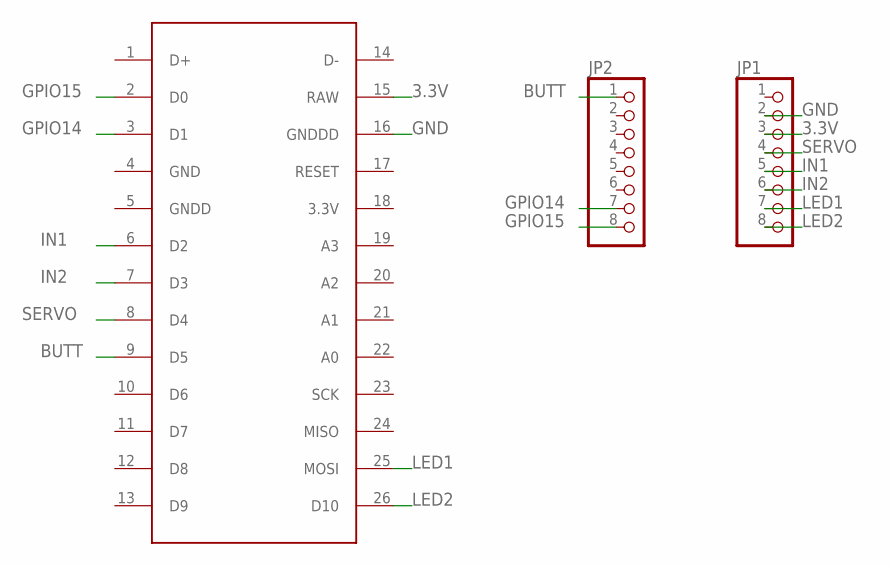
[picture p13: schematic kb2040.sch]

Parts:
JP1, JP2: PINHD-1X8; 1X08
U$1: KB2040

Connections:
3.3V: JP1.3, U$1.15 (RAW)
BUTT: JP2.1, U$1.9 (D5)
GND: JP1.2, U$1.16 (GNDDD)
GPIO14: JP2.7, U$1.3 (D1)
GPIO15: JP2.8, U$1.2 (D0)
IN1: JP1.5, U$1.6 (D2)
IN2: JP1.6, U$1.7 (D3)
LED1: JP1.7, U$1.25 (MOSI)
LED2: JP1.8, U$1.26 (D10)
SERVO: JP1.4, U$1.8 (D4)

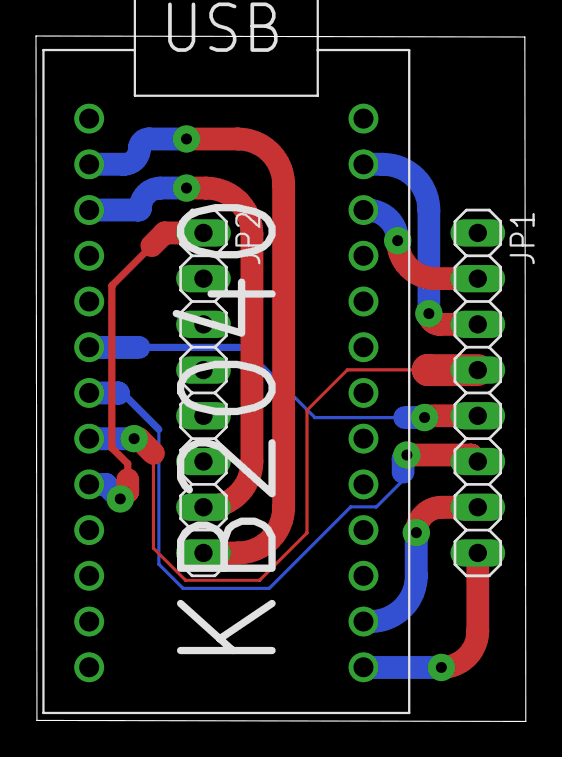
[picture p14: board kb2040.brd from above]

Board: 2 copper layers, 27.2 x 38.1 mm, 3 parts (0 on the bottom side), 10 nets.

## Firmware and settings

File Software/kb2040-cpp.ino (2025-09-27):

#include <Servo.h>

bool motion_flag =true;
bool start_flag = false;
bool start_led = false;
//////////////////////////
#define SERVO_PIN 4
#define MOTOR_PIN_A 2
#define MOTOR_PIN_B 3  
#define BUTTON1_PIN 5
#define BUTTON2_PIN 6
#define LED1_PIN 10
#define LED2_PIN 11

//////////////////////////
Servo myServo;

void setup() {

  pinMode(BUTTON1_PIN, INPUT_PULLDOWN);
  pinMode(BUTTON2_PIN, INPUT_PULLDOWN);
  pinMode(LED1_PIN, OUTPUT);
  pinMode(LED2_PIN, OUTPUT);
  pinMode(MOTOR_PIN_A, OUTPUT);
  pinMode(MOTOR_PIN_B, OUTPUT);
  
  myServo.attach(SERVO_PIN);
  myServo.write(90);
  
  Serial1.begin(9600);
  Serial.begin(115200);
  
  while (Serial1.available()) Serial1.read();
  
  digitalWrite(LED1_PIN, LOW);
  digitalWrite(LED2_PIN, LOW);
  analogWrite(MOTOR_PIN_A, 0);
  analogWrite(MOTOR_PIN_B, 0);
  
}

void loop() {
  bool button1_reading = digitalRead(BUTTON1_PIN);
  bool button2_reading = digitalRead(BUTTON2_PIN);
  if(button1_reading == true){
   start_led = true;
   start_flag = true;
    
  }
  // Handle UART
  if(start_flag){
  if (Serial1.available() > 0) {
    if (start_led){
    digitalWrite(LED1_PIN, HIGH);
    delay(500);
    digitalWrite(LED1_PIN, LOW);    
    start_led = false;
    }
    String cmd = Serial1.readStringUntil('\n');
    cmd.trim();
    if (cmd == "S") {
     myServo.write(100);
      if(motion_flag){
      analogWrite(MOTOR_PIN_A, 0);
      analogWrite(MOTOR_PIN_B, 0);
      
    }
    delay(30000);
    }
    else{
    if (cmd == "F") {
      myServo.write(100);
      if(motion_flag){
      analogWrite(MOTOR_PIN_A, 0);
      analogWrite(MOTOR_PIN_B, 200);
      }
      
    }
    if (cmd == "BR"){
      myServo.write(150);
      analogWrite(MOTOR_PIN_A, 200);
      analogWrite(MOTOR_PIN_B, 0);
    }
    if(cmd == "BL"){
      myServo.write(50);
      analogWrite(MOTOR_PIN_A, 200);
      analogWrite(MOTOR_PIN_B, 0);
    }
    
    if (cmd == "R") {
      myServo.write(140);
      if(motion_flag){
      analogWrite(MOTOR_PIN_A, 0);
      analogWrite(MOTOR_PIN_B, 200);
      }
      
    }
    
    if (cmd == "L") {
      myServo.write(60);
      if(motion_flag){
      analogWrite(MOTOR_PIN_A, 0);
      analogWrite(MOTOR_PIN_B, 200);
      }
    }

    
    if (cmd == "LS") {
      myServo.write(70);
      if(motion_flag){
      analogWrite(MOTOR_PIN_A, 0);
      analogWrite(MOTOR_PIN_B, 200);
      }
    }

    
    if (cmd == "RS") {
      myServo.write(120);
      if(motion_flag){
      analogWrite(MOTOR_PIN_A, 0);
      analogWrite(MOTOR_PIN_B, 200);
      }
    }
    
    if (cmd == "HL") {
     myServo.write(40);
      if(motion_flag){
      analogWrite(MOTOR_PIN_A, 0);
      analogWrite(MOTOR_PIN_B, 255);
      delay(100);
    }
    }
    //-160, -7, -210
    //-116, 151 , -312
    if (cmd == "HR") {
     myServo.write(160);
      if(motion_flag){
      analogWrite(MOTOR_PIN_A, 0);
      analogWrite(MOTOR_PIN_B, 255);
      delay(100);
    }
    }
    if (cmd == "LC"){
      myServo.write(50);
      analogWrite(MOTOR_PIN_A, 0);
      analogWrite(MOTOR_PIN_B, 200);
    }
    if (cmd == "RC"){
      myServo.write(150);
      analogWrite(MOTOR_PIN_A, 0);
      analogWrite(MOTOR_PIN_B, 200);
    }
    
  }
  
}
}
}

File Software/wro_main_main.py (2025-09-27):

from ultralytics import YOLO
import cv2
import numpy as np
from libcamera import controls
from picamera2 import Picamera2
from time import sleep
import serial 
import time
from gpiozero import DistanceSensor

ultrasonic1 =0#DistanceSensor(echo=20,trigger=6) #,pin_factory=factory
ultrasonic2 =0#DistanceSensor(echo=21,trigger=26)


ser = serial.Serial('/dev/ttyAMA2',9600, timeout=1)
ser.reset_input_buffer()

ser2 = serial.Serial('/dev/ttyAMA0',9600, timeout=1)
ser2.reset_input_buffer()

picam2 = Picamera2(0)
picam2.preview_configuration.main.size=(640,640) #full screen : 3280 2464
picam2.preview_configuration.main.format = "RGB888" #8 bits
picam2.start()

model = YOLO("/home/pi/yolo/model_- 24 september 2025 0_49_edgetpu.tflite", task='detect') 

orange_corner = False
blue_corner = False

see_black_left = False
see_black_right = False

go_back = False

back_right = False
back_left = False

counter = 0
dist_counter = 0

corner_flag = False

box_flag = False

saw_red, saw_green = False, False

"""
hoigher =  (179, 164, 72)
lower =  (0, 0, 27)

"""

black_lower = np.array([0, 0, 27], np.uint8)
black_upper =np.array([179, 164, 72], np.uint8)
def left_wall(frame):
   
    cropped_image = frame[290:380,20:110]
    global black_lower
    global black_upper
    global see_black_left
    global back_left
    cv2.rectangle(im, (20,290),(110,380),(0,255,0),4) #green region
    
    hsvf = cv2.cvtColor(cropped_image, cv2.COLOR_BGR2HSV)
    black_mask = cv2.inRange(hsvf, black_lower, black_upper)
    black_result = cv2.bitwise_and(cropped_image, cropped_image, mask=black_mask)
    black_contours, black_hierarchy = cv2.findContours(black_mask, cv2.RETR_TREE, cv2.CHAIN_APPROX_SIMPLE)
    if len(black_contours) > 0:
        largest_black = max(black_contours, key=cv2.contourArea)
        area = cv2.contourArea(largest_black)
        cv2.drawContours(cropped_image, largest_black, -1, (255, 0, 0), 3)
        x, y, w, h = cv2.boundingRect(largest_black)
        #area = w*h
        #cv2.rectangle(cropped_image,(x,y),(x+w,y+h), (220,220,220), 2)
        if 6500>area:
            see_black_left = True
            back_left = False
            return area//10
        if area >=6500:
            back_left = True
            return area//10
        else:
            see_black_left = False
            back_left = False
            return 0
        
    else:
        see_black_left = False
        return 0


def right_wall(frame):
    cropped_image = frame[290:380,530:620]#frame[230:350,455:545]
    global black_lower
    global black_upper
    global see_black_right
    global back_right
    cv2.rectangle(im, (530,290),(620,380),(0,255,0),4) #green region
    #for i,region in enumerate(cropped_image):
    hsvf = cv2.cvtColor(cropped_image, cv2.COLOR_BGR2HSV)
    black_mask = cv2.inRange(hsvf, black_lower, black_upper)
    black_result = cv2.bitwise_and(cropped_image,cropped_image, mask=black_mask)
    black_contours, black_hierarchy = cv2.findContours(black_mask, cv2.RETR_TREE, cv2.CHAIN_APPROX_SIMPLE)
    if len(black_contours) > 0:
        see_black_right = True
        largest_black = max(black_contours, key=cv2.contourArea)
        selected_black=largest_black
        area = cv2.contourArea(selected_black)
        cv2.drawContours(cropped_image, largest_black, -1, (255, 0, 0), 3)
        x, y, w, h = cv2.boundingRect(largest_black)
        #area = w*h
        #cv2.rectangle(cropped_image,(x,y),(x+w,y+h), (220,220,220), 2)
        if 6500>area:
            back_right = False
            return area//10
        if area>=6500:
            back_right = True
            return area//10
            
        else:
            back_right = False
            see_black_right = False
            return 0
    else:
        see_black_right = False
        return 0


def middle_region(frame):
    cropped_image = frame[280:450,280:520]#frame[230:350,455:545]
    global black_lower
    global black_upper
    global see_black_middle, go_back
    #cv2.rectangle(im, (120,280),(520,450),(0,255,0),4) #left region
    #for i,region in enumerate(cropped_image):
    hsvf = cv2.cvtColor(cropped_image, cv2.COLOR_BGR2HSV)
    black_mask = cv2.inRange(hsvf, black_lower, black_upper)
    black_result = cv2.bitwise_and(cropped_image,cropped_image, mask=black_mask)
    black_contours, black_hierarchy = cv2.findContours(black_mask, cv2.RETR_TREE, cv2.CHAIN_APPROX_SIMPLE)
    if len(black_contours) > 0:
        
        largest_black = max(black_contours, key=cv2.contourArea)
        
        area = cv2.contourArea(largest_black)
        cv2.drawContours(cropped_image, largest_black, -1, (255, 0, 0), 3)
        x, y, w, h = cv2.boundingRect(largest_black)
        #area = w*h
        #cv2.rectangle(cropped_image,(x,y),(x+w,y+h), (220,220,220), 2)
        
        if area>=16000:
            go_back = True
            return area//10
            
        else:
            go_back = False
            return 0
    else:
        
        return 0


def blue(frame):
    global blue_corner
    cropped_image = frame[500:550,200:480]#frame[230:350,455:545]
    """
    hoigher =  (121, 199, 139)
    lower =  (92, 121, 35)

    """
    blue_lower = np.array([92, 121, 35], np.uint8)
    blue_upper =np.array([121, 199, 139], np.uint8)
    #for i,region in enumerate(cropped_image):
    hsvf = cv2.cvtColor(cropped_image, cv2.COLOR_BGR2HSV)
    blue_mask = cv2.inRange(hsvf, blue_lower, blue_upper)
    blue_result = cv2.bitwise_and(cropped_image,cropped_image, mask=blue_mask)
    blue_contours, blue_hierarchy = cv2.findContours(blue_mask, cv2.RETR_TREE, cv2.CHAIN_APPROX_SIMPLE)
    if len(blue_contours) > 0:
        largest_blue = max(blue_contours, key=cv2.contourArea)
        area = cv2.contourArea(largest_blue)
        cv2.drawContours(cropped_image, largest_blue, -1, (255, 0, 0), 3)
        x, y, w, h = cv2.boundingRect(largest_blue)
        if area >= 100:
            blue_corner = True
            
        #area = w*h
        #cv2.rectangle(cropped_image,(x,y),(x+w,y+h), (220,220,220), 2)
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

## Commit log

2025-09-16 Added design files for the robot.
    [Base.SLDPRT, WRO_2025 PCB.SLDASM]
2025-09-16 Add qualification_code.py for navigation and detection
    This script utilizes a camera and ultrasonic sensors to navigate and detect colored corners, controlling a device based on sensor input.
2025-09-16 Added .brd and .sch files for the robot
    [Data Cable REPLACMENT.brd, Data Cable REPLACMENT.sch, WRO_2025.brd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]
2025-09-16 Add camera test script using Picamera2 and OpenCV
2025-09-16 Add Serial_communication.py for yaw control
    Implement serial communication for yaw angle control.
2025-09-16 Add ultrasonic sensor test script
2025-09-16 Add motor control and servo setup
    Implement motor control and servo positioning in motor_testing.ino
2025-09-16 Add MPU6050 sensor test code
    This code initializes and configures the MPU6050 sensor, enabling its Digital Motion Processor (DMP) and reading yaw, pitch, and roll values in a loop.
2025-09-27 Enhance README with details on schematics and boards
    Added a brief description of schematic and board files.
2025-09-27 Update README with box detection and code flow details
    Expanded README to include box detection and general flow of code.
2025-10-28 Enhance README with robot design details
    Added detailed sections on robot architecture, design philosophy, system diagram, and bill of materials.
2025-10-28 Update README with testing and future improvements
    Added testing and calibration details to README.
2025-11-06 Revise README with Raspberry Pi details and algorithms
    Updated README to reflect changes in the Raspberry Pi system and added detailed explanations for the complementary filter and PID controller implementations.
2025-11-06 Update Block Diagram section to Flow Chart
2025-11-07 Fix voltage intensity graph image source
    Updated image source for voltage intensity graph in README.
2025-11-07 Fix image tag for voltage intensity graph
2025-11-07 Add Raspberry Pi setup script for AI environment
    This script sets up a Raspberry Pi environment with I2C, Python, NumPy, OpenCV, and Coral TPU Runtime.
2025-11-07 Add Raspberry Pi setup script instructions to README
    Added a note about the Raspberry Pi setup script for easier reproduction of the robot.
2025-11-07 Revise README for mechanical design details
    Updated the README to provide detailed descriptions of the mechanical design, including the drive and steering systems, along with images.
2025-11-07 added all updated files
    [!Assem_v2.SLDASM, Base_v2.SLDPRT]
